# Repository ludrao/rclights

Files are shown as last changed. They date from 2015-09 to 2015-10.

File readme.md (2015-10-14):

# RC Lights control system

### Basic feature list:
* Two On/Off (PWM) outputs (fronts lights and rear lights)
* Two inputs (radio signal) (engine, and lights switch)
* One setup button.

### More descriptive feature:
The system captures the engine level, and switch on the rear lights when breaking. The lights switch (on a 3rd chanel) allows to switch on/off the front lights and the rear lights at 30% power (night mode).

The current software works for a RC Lights control system.

However, the hardware platform could be retrofited for any uses cases requirering 2 PWM outputs and 2 IN/OUT radio signal channels.
It is based on a PIC 12F1840, programmable directly in C (I used MPLABX for this project...)

### Some hardware details:
* MCU is a PIC12F1840, low power
* MCU powered at 3.3V linear regulator (ideally LDO to support low BEC)
* The two output have BS170 (N-Mosfet) supporting up to 500mA continuous load

The PCB is single face, with through hole components. It could be easily be converted int a surface mount PCB, thus reducing further the size of the PCB (basically the size of the button+connector). Please let me know if you are interested...

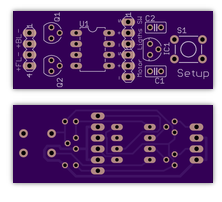
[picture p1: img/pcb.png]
alt test PCB, only one face


Here is an export of the schematic (the sources files are in Eagle format in the hw directory).
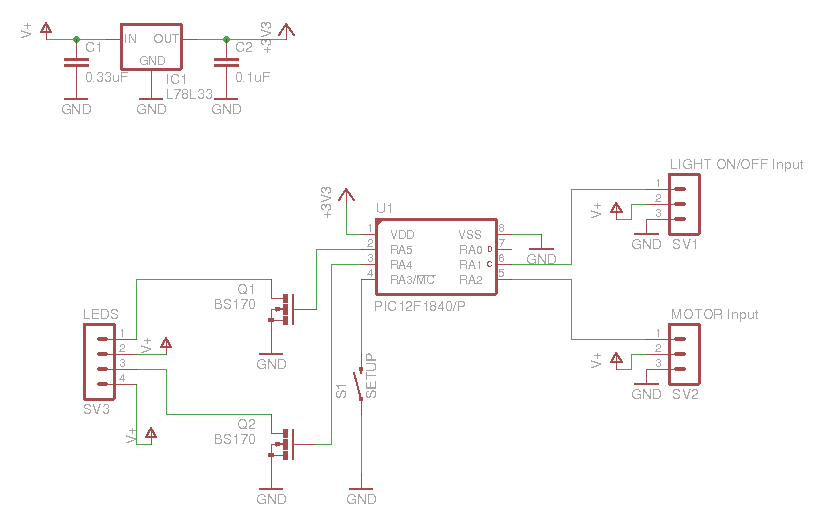
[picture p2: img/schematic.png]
alt test schematic export


The full system, assembled and under test on my TB-04 Chassis...
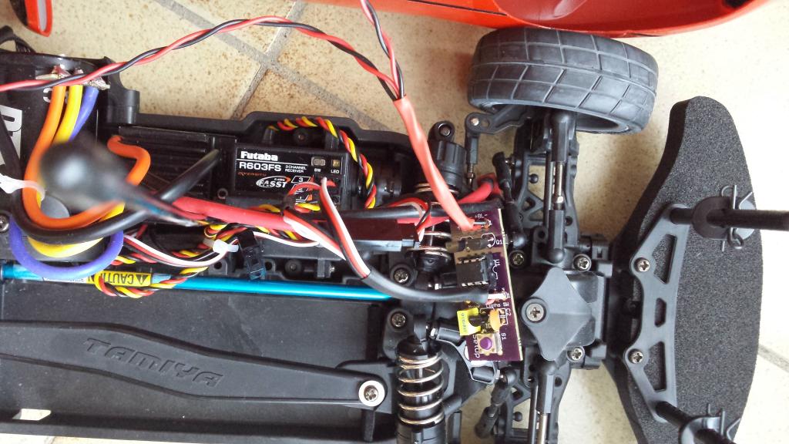
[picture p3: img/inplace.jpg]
alt test The system in test...


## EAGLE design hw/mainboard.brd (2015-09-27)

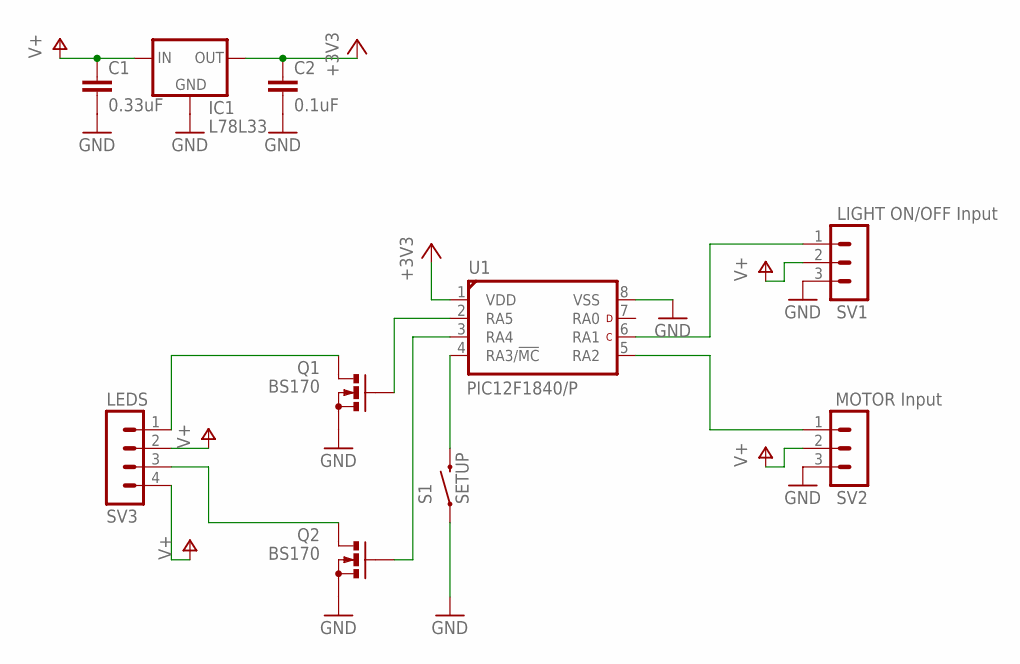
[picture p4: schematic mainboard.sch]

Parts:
C1: 0.33uF; C025-025X050
C2: 0.1uF; C025-025X050
IC1: L78L33; 78LXX
Q1, Q2: BS170; SOT54E
S1: SETUP; TACTILE-PTH
SV1: LIGHT ON/OFF Input; MA03-1
SV2: MOTOR Input; MA03-1
SV3: LEDS; MA04-1
U1: PIC12F1840/P; DIL8-P

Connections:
+3V3: C2.1, IC1.OUT, U1.1 (VDD)
GND: C1.2, C2.2, IC1.GND, Q1.S, Q2.S, S1.1, SV1.3, SV2.3, U1.8 (VSS)
unnamed: Q1.D, SV3.1
unnamed: Q1.G, U1.2 (RA5)
unnamed: Q2.G, U1.3 (RA4)
unnamed: Q2.D, SV3.3
unnamed: SV2.1, U1.5 (RA2)
unnamed: SV1.1, U1.6 (RA1)
unnamed: S1.3 (2), U1.4 (RA3/!MC!)
V+: C1.1, IC1.IN, SV1.2, SV2.2, SV3.2, SV3.4

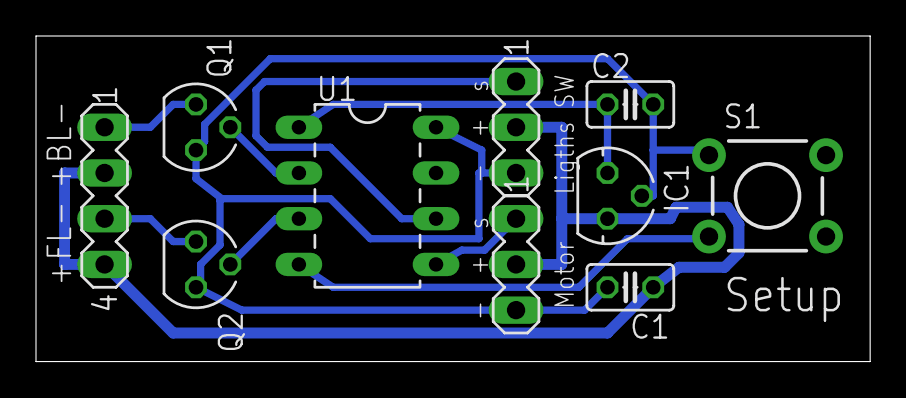
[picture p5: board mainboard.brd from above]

Board: 2 copper layers, 46.3 x 18.1 mm, 10 parts (0 on the bottom side), 10 nets.

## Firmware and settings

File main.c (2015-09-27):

/* 
 * File:   main.c
 * Author: cuero
 *
 * Created on 19 janvier 2014, 18:36
 */

// PIC12F1840 Configuration Bit Settings

// 'C' source line config statements

// Crap to remove warning in the IDE...
//#ifndef __PICCPRO__
//#define __PICCPRO__
//#endif
//#ifndef EEPROM_SIZE
//#define EEPROM_SIZE
//#endif
// End of Crap

#define _XTAL_FREQ 16000000 // used for __delay_ms macro

#include <xc.h>


// #pragma config statements should precede project file includes.
// Use project enums instead of #define for ON and OFF.

// CONFIG1
#pragma config FOSC = INTOSC    // Oscillator Selection (INTOSC oscillator: I/O function on CLKIN pin)
#pragma config WDTE = OFF       // Watchdog Timer Enable (WDT enabled)
#pragma config PWRTE = OFF      // Power-up Timer Enable (PWRT disabled)
#pragma config MCLRE = OFF      // MCLR Pin Function Select (MCLR/VPP pin function is Digital Input)
#pragma config CP = OFF         // Flash Program Memory Code Protection (Program memory code protection is disabled)
#pragma config CPD = OFF        // Data Memory Code Protection (Data memory code protection is disabled)
#pragma config BOREN = ON       // Brown-out Reset Enable (Brown-out Reset enabled)
#pragma config CLKOUTEN = OFF   // Clock Out Enable (CLKOUT function is disabled. I/O or oscillator function on the CLKOUT pin)
#pragma config IESO = OFF       // Internal/External Switchover (Internal/External Switchover mode is disabled)
#pragma config FCMEN = ON       // Fail-Safe Clock Monitor Enable (Fail-Safe Clock Monitor is enabled)

// CONFIG2
#pragma config WRT = OFF        // Flash Memory Self-Write Protection (Write protection off)
#pragma config PLLEN = OFF      // PLL Enable (4x PLL disabled)
#pragma config STVREN = ON      // Stack Overflow/Underflow Reset Enable (Stack Overflow or Underflow will cause a Reset)
#pragma config BORV = LO        // Brown-out Reset Voltage Selection (Brown-out Reset Voltage (Vbor), low trip point selected.)
#pragma config LVP = OFF        // Low-Voltage Programming Enable (Low-voltage programming disabled)




// EEPROM layout:
// 0 : neutral position 
__EEPROM_DATA(125, 0, 0, 0, 0, 0, 0, 0); // Define EEPROM initial data. Here Only the First value is used

unsigned char neutral;

void init()
{

    // Configure Oscillator
    // Set the system clock to 16MHz
    OSCCONbits.IRCF = 0xF;


    // Configure Ports (IO)
    LATA = 0;   // Set IO to 0
    ANSELA = 0; // no alog inputs

    // RA1 is the 3rd channel RC signal (Light On/Off control) (with weak pull up)
    // RA2 is the motor RC signal (input) (with Weak Pull Up)
    // RA3 is the button input (setup button) (with Weak Pull Up)
    // RA4 is front light  (output)
    // RA5 is brake light  (output as PWM)
    // Other IOs as inputs
    TRISA = 0x0F;
    WPUA = 0x0E; // RA1, RA2, RA3 weak pull up enabled
    OPTION_REGbits.nWPUEN = 0; // Enable weak pull ups


    // Setup RA5 PWM
    APFCONbits.CCP1SEL = 1; // RA5 is CCP1 pin (PWM output)
    // PWM frequency is set to 0,9765625 (16MHz/(4*(PR2+1)*16)
    PR2 = 0xFF;
    T2CONbits.T2CKPS = 2; // prescaler of 16
    T2CONbits.TMR2ON = 1; // start timer
    CCP1CONbits.P1M = 0;



    // Set up interupts on Inputs pins (RA1, RA2) (Interupt-On-Change)
    INTCONbits.IOCIE = 1;
    IOCAP = 0x6; // enable rising edge detection on both RA1, RA2
    IOCAN = 0x0; // No falling edge detection for now!

    // Setup Timer 1
    T1CONbits.TMR1CS = 0; // Use FOSC/4 as clock source (=4MHz)
    T1CONbits.T1CKPS = 0; // No prescaler
    T1CONbits.TMR1ON = 1; // Start Timer1 !

    // Initialize the neutral position
    neutral = eeprom_read(0);
}






// Percentage for RA1 and RA2 channels (computed in the ISR) 0 (1ms pulse) to 250 (2ms pulse)
// 0 -> RA1 (CH3)
// 1 -> RA2 (Throttle/Brake)
unsigned char si[2] = {255, 255};

void interrupt isr(void)
{
    // Timestamps to measure pulse width
    static unsigned short RA_ts[2];

    unsigned short ts = TMR1; // store timer1 value as soon as the interuption is processed


    if(INTCONbits.IOCIF)
    {// Interrupt-On-Change Interrupt

        for (int i = 1; i<=2; i++)
        {
            unsigned char m = 1<<i;
            
            if (IOCAF & m)
            {// RAx changed
                if (IOCAP & m)
                {   // It is a rising edge
                    // Store rising edge timestamp
                    RA_ts[i-1] = ts;
                }
                else
                {   // It is a falling edge
                    // Measure elapsed time since last rising edge
                    // Compute RAx_p into a 0-250 range
                    unsigned short pw = ts - RA_ts[i-1];
                    if (pw < 4000) pw = 4000;
                    if (pw > 8000) pw = 8000;
                    si[i-1] = (unsigned char)((pw-4000)/16);
                }
                // Inverse edge detection
                IOCAP ^= m;
                IOCAN ^= m;
            }
        }

        // Reset all input interrupts flags
        IOCAF = 0;
        INTCONbits.IOCIF = 0; // clear the IOC interupt flag
    }
}

void setupmode()
{
    // Rapidly blink Front Light to signify the setup mode
    for (int i = 0 ; i<5 ; i++)
    {
        LATA4 = 1;
        __delay_ms(50);
        LATA4 = 0;
        __delay_ms(50);
    }

    // measure and store the new neutral position
    neutral = si[1];
    eeprom_write(0, neutral);
}



int main(void) {

    init();

    // Blink front / rear leds at startup
    LATA = 0x30;
    __delay_ms(150);
    LATA = 0x0;
    __delay_ms(150);

    // Init done, enable interupts!
    INTCONbits.GIE = 1;

    unsigned short db_count = 0;

    // Wait for engine signal detection
    unsigned char c = 0;
    unsigned char d = 1;
    while (si[1] == 255)
    {
        unsigned char i;
        for(i=0; i!=255; i++)
        {
            if (c<i)
                LATA = 0x10;
            else
                LATA = 0x20;
            __delay_us(3);
        }
        if ((c==0 && d<0) || (c==255 && d>0))
            d=-d;

        c += d;

    }

    // Activate PWM: BackLight at 30% (RA5)
    CCP1CONbits.CCP1M = 0b1100; // Configure as a single output active high PWM
    CCPR1L = 0x40;
    CCP1CONbits.DC1B = 0x0;

    // Switch on front light (RA4) on
    LATA4 = 1;

    // main loop
    while(1)
    {
        unsigned char lighton = 0;
        __delay_ms(1); // no need to loop faster than once evey 1 ms!


        // Enter in setup mode if the button is pressed more than 1 second
        if (!PORTAbits.RA3)
        {

            db_count++;
            if (db_count > 1000)
            {
                setupmode();
                db_count = 0;
            }
        }
        else
            db_count = 0;


        // Switch on the On/Off of the lights
        if (si[0] < 100)
            lighton = 1;
        else if (si[0] > 150)
            lighton = 0;

        // Set RA4 according to the light state
        LATA4 = lighton;


        // Control the rear light
        if (si[1] < neutral-23) // If pulse width is small enough (means braking)
        {
            // Switch on brake light to 100%
            CCPR1L = 0xFF;
            CCP1CONbits.DC1B = 0x3;
        }
        else if (si[1] >= neutral-5)
        {
            // If lights are on => rear lights on
            if (lighton)
            {
                // Switch back/brake light to ~30%
                CCPR1L = 0x40;
                CCP1CONbits.DC1B = 0x0;
            }
            else
            {
                // Switch back/brake light to 0%
                CCPR1L = 0x0;
                CCP1CONbits.DC1B = 0x0;
            }
        }
    }
    
    return 0;
}

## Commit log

2015-09-27 First load of the project
    [leds.sch, mainboard.brd, mainboard.sch]
2015-09-27 Add readable schematic export in readme.md

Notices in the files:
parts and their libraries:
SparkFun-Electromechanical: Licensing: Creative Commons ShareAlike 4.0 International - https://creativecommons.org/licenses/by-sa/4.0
